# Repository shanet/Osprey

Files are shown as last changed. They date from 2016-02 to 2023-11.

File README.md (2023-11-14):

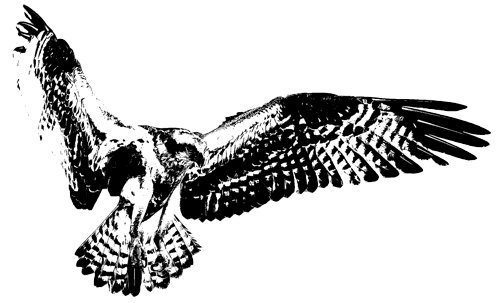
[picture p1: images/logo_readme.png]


Osprey
======

**Note: I am no longer active in rocketry and as such this repo is unmaintained. Everything here is fairly self-enclosed, however, so it should be possible to get running without too much trouble if you are interested in it.**

Osprey is a free and open source tracking, telemetry, and dual deployment system for amateur rocketry utilizing only off-the-shelf components. It consists of five major components:

0. [The microcontroller and associated sensors](docs/arm.md)
0. [The e-match igniter circuit](docs/igniter.md)
0. [The Android application for receiving data during a flight](docs/android.md)
0. [The desktop application for laptop-based analysis and debugging](docs/desktop.md)
0. [The launch report generation script for post-flight analysis](docs/reports.md) ([sample launch report](https://shanet.github.io/Osprey/))

The final assembled product, corresponding Android application, and launch report:

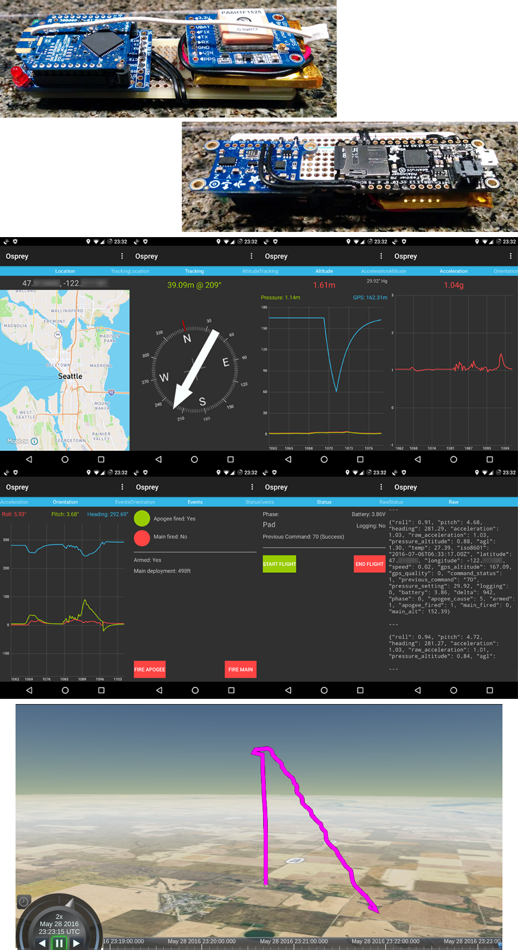
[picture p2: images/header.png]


The following data is collected:

| | | | |
|---|---|---|---|
|Latitude & longitude |Above ground level |ISO 8601 timestamp  |Battery voltage |
|Roll, pitch, heading |Pressure altitude |Integer timestamp |Temperature |
|Acceleration |GPS altitude & speed |Flight phase |Event fired flags |

All data is logged to an on-board microSD card and transmitted via radio to the Android application.

## High Level Build Overview

Osprey, by nature, is extremely DIY. This is necessary to achieve its goal of not using any custom printed hardware or non-free software. If you are not comfortable soldering your own circuits together or compiling software from source, this is not the project for you. In fact, it's quite likely, even inevitable, that something won't go as intended during a build. Those looking for a more plug'n'play solution should look elsewhere. For the adventurous out there, to fully construct everything follow these steps:

0. [Assemble the microcontroller and associated sensors](docs/arm.md)
0. [Assemble the igniter board](docs/igniter.md)
0. [Compile and upload the microcontroller software](docs/arm.md#software)
0. [Set the required radio configuration](docs/radio.md)
0. [Install the completed microcontroller, sensors, igniter, and switch to your e-bay sled](docs/assembly.md)
0. [Compile and install the Android application](docs/android.md)
0. [Review the usage section](docs/usage.md)
0. Do some ground tests, then stick it in a rocket and cross your fingers.

For everything else, see the documentation in the `docs` directory.

A write-up of some of Osprey's internals (Kalman filter, apogee detection, testing, etc.) is [available on my blog](https://shanetully.com/2016/07/inside-the-construction-of-an-amateur-rocketry-flight-computer).

## Roadmap

Some potential future additions:

* "Micro version" with only a processor, IMU, and battery for data logging purposes only.
* The 3D flight path playback in the launch report could be made more rich with the addition of altitude and flight phase data.
* Support for multiple flight stages.
* Reworking the igniter circuit to only need a single capacitor.
* Support for offline maps in the generated launch report webpage.

## Contributing

Pull requests, bug reports, and general questions are welcome. Additionally, suggestions on where the documentation can be made more clear are extremely useful. Log files and generated launch reports are appreciated as well for helping to improve the project and as a showcase.

## License

This program is free software: you can redistribute it and/or modify
it under the terms of the GNU General Public License as published by
the Free Software Foundation, either version 3 of the License, or
(at your option) any later version.

This program is distributed in the hope that it will be useful,
but WITHOUT ANY WARRANTY; without even the implied warranty of
MERCHANTABILITY or FITNESS FOR A PARTICULAR PURPOSE.  See the
GNU General Public License for more details.

You should have received a copy of the GNU General Public License
along with this program.  If not, see <http://www.gnu.org/licenses/>.

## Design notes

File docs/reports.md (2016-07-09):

## Launch Reports

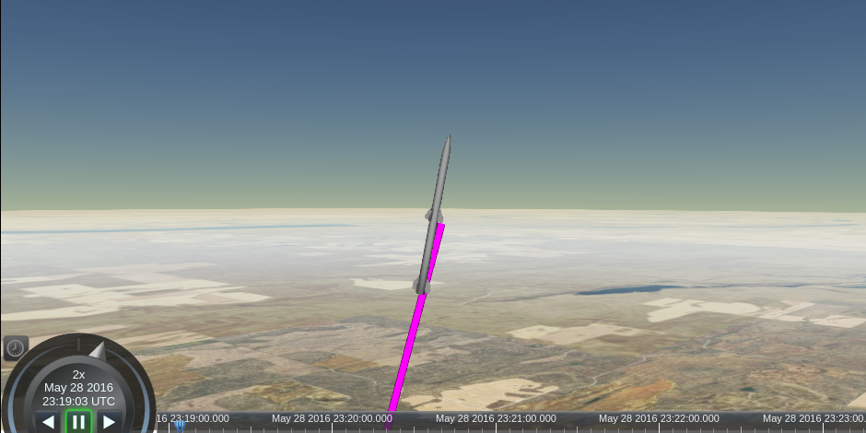
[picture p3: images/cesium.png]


A Ruby script to generate a self-contained, static HTML report of a launch from its log file is included. This allows for quick analysis of a flight including the following information:

| | | |
|---|---|---|
|Actual apogee |Calculated apogee |Apogee cause |
|Main chute target |Main chute actual |Average temperature |
|Flight time |Ascent time |Ascent rate |
|Descent time |Descent rate - drogue |Descent rate - main |

And:
* Graph of altitude, acceleration, and ground speed vs. time
* 3D view of flight path and rocket orientation (roll, pitch, heading)

[See here for a sample launch report](https://shanet.github.io/Osprey/)

### Dependencies

* Ruby (any recent version should do; no gems are required)

### Usage

```
$ reports/generate.rb
Usage: reports/generate.rb [input log] [output directory]
```

Then open `output_directory/report.html` in any web browser that supports WebGL. Chrome users: Chrome must be started with the `--allow-file-access-from-files` flag for the 3D playback to work.

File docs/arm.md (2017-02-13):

## Microcontroller & Sensors

All assembled, the total size is 9.5cm x 3.3cm x 2.8cm and weighs in at 50g.

### Hardware

The following hardware is used:

* [Adafruit Feather M0 Adalogger](https://www.adafruit.com/products/2796)
* [Adafruit Ultimate GPS](https://www.adafruit.com/products/746)
* [Adafruit 10-DOF IMU](https://www.adafruit.com/products/1604)
* [XBee Pro 900 Wire Antenna](http://www.mouser.com/ProductDetail/Digi-International/XBP9B-DMWT-002)
* [XBee Pro 900 RP-SMA Connector](http://www.mouser.com/ProductDetail/Digi-International/XBP9B-DMST-002)
* [Adafruit XBee Adapter Kit](https://www.adafruit.com/product/126)
* [SparkFun XBee Explorer Dongle](https://www.sparkfun.com/products/11697)
* [Adafruit 500mAh LiPo battery](https://www.adafruit.com/product/1578)
* [Adafruit Perma-Proto Half-size Breadboard PCB](https://www.adafruit.com/products/1609) (cut in half for use as a mounting board)
* Either an omnidirectional antenna or a Yagi antenna with an RP-SMA connector
* [3 position terminal block](https://www.adafruit.com/products/725)
* USB OTG if connecting to an Android device
* [Foam mounting tape to hold everything to the mounting board](https://www.amazon.com/3M-Scotch-Mounting-125-Inch-314/dp/B0007P5G8Y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)

**Note:** Adafruit is occasionally out of stock with their components. I have had good luck in the past finding them in stock at [Mouser](http://www.mouser.com).

### Wiring

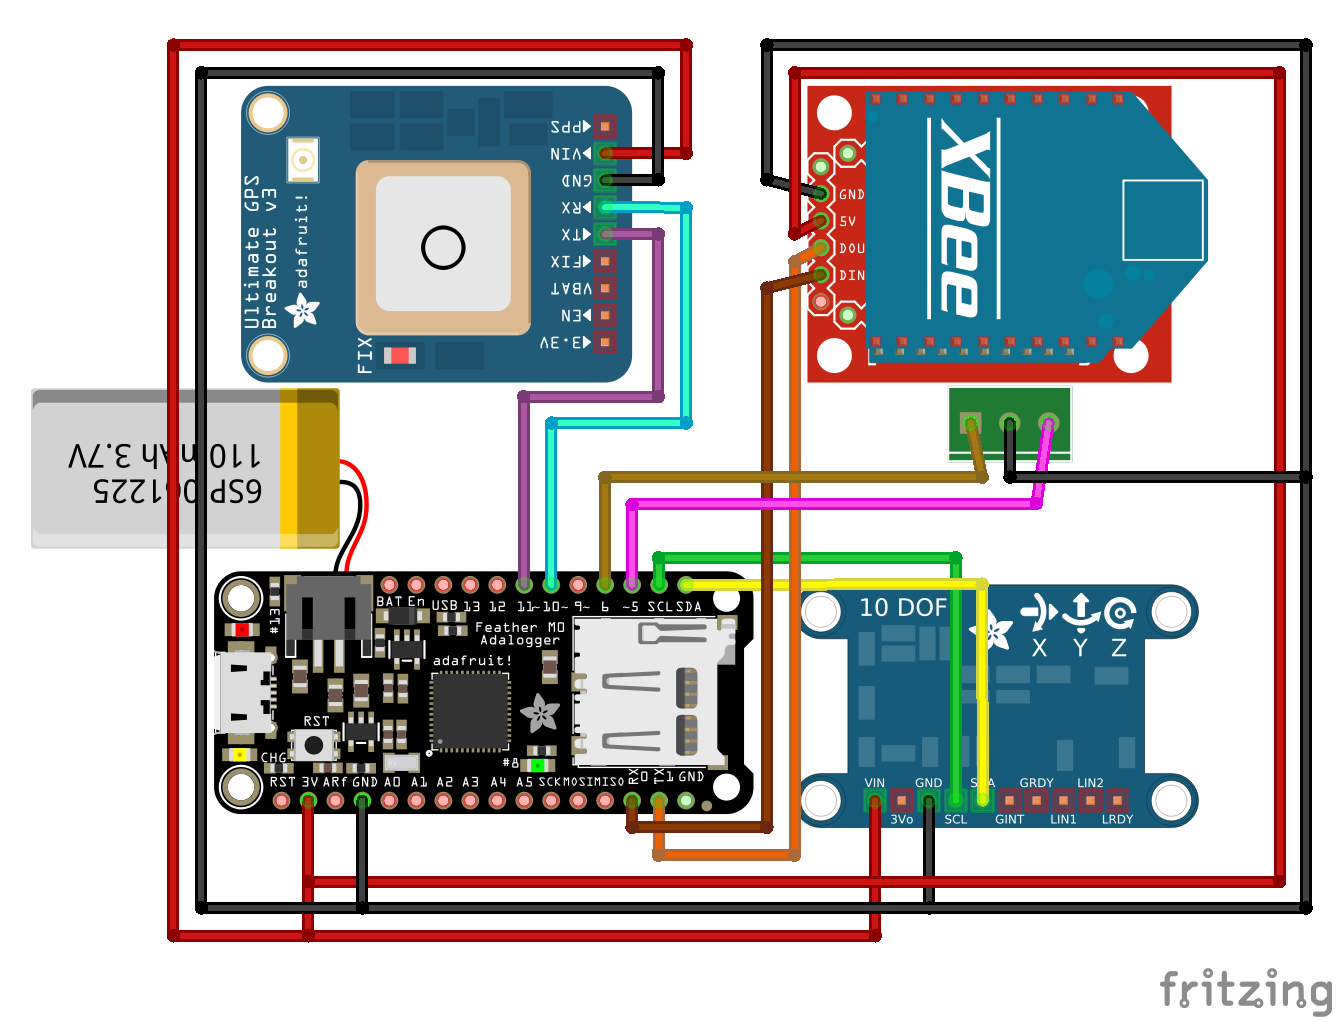
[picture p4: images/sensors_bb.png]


|Radio | GPS | IMU | Igniter terminal |
|---|---|---|---|
|Pin 1 -> RX | Pin 10 -> RX | SDA -> SDA  | Left -> Pin 6 |
|Pin 0 -> TX | Pin 11 -> TX | SCL -> SCL  | Center -> GND |
|3.3V -> Vin | 3.3V -> Vin  | 3.3V -> Vin | Right -> Pin 5 |
|GND -> GND  | GND -> GND | GND -> GND  | |

### Software

#### Dependencies

These instructions are for Linux (x86_64). See below for where to find instructions for other platforms. Do not ask for Windows support.

* Download and extract the [Adafruit SAMD library](https://github.com/adafruit/arduino-board-index/raw/gh-pages/boards/adafruit-samd-1.0.9.tar.bz2) to `~/.arduino15/packages/adafruit/hardware/samd/1.0.9`
* Download and extract the [ARM compiler](http://downloads.arduino.cc/gcc-arm-none-eabi-4.8.3-2014q1-linux64.tar.gz) to `~/.arduino15/packages/adafruit/tools/arm-none-eabi-gcc/4.8.3-2014q1`
* Download and extract [Bossac](http://downloads.arduino.cc/bossac-1.6.1-arduino-x86_64-linux-gnu.tar.gz) to `~/.arduino15/packages/adafruit/tools/bossac/1.6.1-arduino`.
* Download and extract [CMSIS](http://downloads.arduino.cc/CMSIS-4.0.0.tar.bz2) to `~/.arduino15/packages/adafruit/tools/CMSIS/4.0.0-atmel`.

Note: The archives above can be extracted whenever you'd like, but the paths at the top of the Makefile must be adjusted accordingly.

Alternatively, Adafruit has good instructions for getting the above set up with the help of the Arduino software. If not using Linux, this is most likely the easiest way to gather the dependencies.

For convenience, here's a list of commands to download each of the tarballs above and put them in the correct location:

```
mkdir -p ~/.arduino15/packages/adafruit/hardware/samd/1.0.9
mkdir -p ~/.arduino15/packages/adafruit/tools/arm-none-eabi-gcc/4.8.3-2014q1
mkdir -p ~/.arduino15/packages/adafruit/tools/bossac/1.6.1-arduino
mkdir -p ~/.arduino15/packages/adafruit/tools/CMSIS/4.0.0-atmel

curl --location https://github.com/adafruit/arduino-board-index/raw/gh-pages/boards/adafruit-samd-1.0.9.tar.bz2 | tar -xjf - --strip-components=1 --directory ~/.arduino15/packages/adafruit/hardware/samd/1.0.9
curl http://downloads.arduino.cc/gcc-arm-none-eabi-4.8.3-2014q1-linux64.tar.gz | tar -xzf - --strip-components=1 --directory ~/.arduino15/packages/adafruit/tools/arm-none-eabi-gcc/4.8.3-2014q1
curl http://downloads.arduino.cc/bossac-1.6.1-arduino-x86_64-linux-gnu.tar.gz | tar -xzf - --strip-components=1 --directory ~/.arduino15/packages/adafruit/tools/bossac/1.6.1-arduino
curl http://downloads.arduino.cc/CMSIS-4.0.0.tar.bz2 | tar -xjf - --strip-components=1 --directory ~/.arduino15/packages/adafruit/tools/CMSIS/4.0.0-atmel

```

#### Compiling & Uploading

```
$ cd arm
$ make
$ make upload
```

### Tests

```
$ cd arm
$ make test
$ make test_run # Don't re-compile, only run tests
```

#### Replaying flight from log

In some cases, it is useful to "replay" a flight from its associated log file. For example, when working on logic for apogee detection it is much easier and faster to replay the flight from an existing log file instead of doing actual test launches. To use this, simply place a log file at
```
arm/test/fixtures/replay.json
```
and then run the tests as normal. The output from the replayed flight will be printed to stdout in the usual log format.

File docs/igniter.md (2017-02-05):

## Igniter

Osprey uses a custom designed, capacitor-based igniter circuit with two channels and capable of being powered by a 3.7V lipo battery. **This is an optional component.** It is perfectly okay to simply skip this for use in a non-dual deployment or low power rocket. The microcontroller itself can fit inside a 1.65" diameter rocket which makes for a great standalone tracking system.

All assembled, the total size is 8.2cm x 2.5cm x 2.1cm and weighs in at 26g.

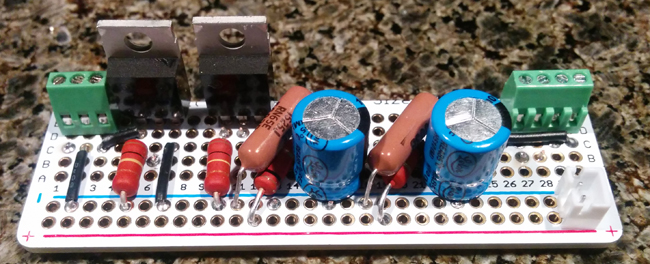
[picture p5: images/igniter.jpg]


### Hardware

* [30V 30A N-channel MOSFET x2](http://www.mouser.com/ProductDetail/NXP/PSMN022-30PL127/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)
* [1000uF capacitor x2](http://www.mouser.com/ProductDetail/Lelon/REA102M1ABK-1012P/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)
* [500k Ohm resistor x2](http://www.mouser.com/ProductDetail/Vishay/RN65E5003BB14/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)
* [100k Ohm resistor x2](http://www.mouser.com/ProductDetail/Vishay-BC-Components/PR02000201003JR500/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)
* [1k Ohm resistor x2](http://www.mouser.com/ProductDetail/Vishay-BC-Components/PR02000201001JR500/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)
* [3-position terminal block](http://www.mouser.com/ProductDetail/Adafruit/2136/)
* [4-position terminal block](http://www.mouser.com/Search/ProductDetail.aspx?qs=GURawfaeGuCecymQwHHL1g%3d%3d)
* JST-PH connector for battery
* [JST-PH Breakout board](https://www.adafruit.com/product/1862)
* [Magnetic switch](http://shop.featherweightaltimeters.com/product.sc?productId=33&categoryId=2).
** Magnets: I used a combination of both a [cube magnet](https://www.amazon.com/gp/product/B0012DNFP6/ref=oh_aui_search_detailpage?ie=UTF8&psc=1) and [circular magnets](https://www.amazon.com/gp/product/B008H40U10/ref=oh_aui_search_detailpage?ie=UTF8&psc=1).

### Switch

Any switch will work; I used a magnetic switch for the ability to easily turn the electronics on/off without the need to put a large access hole in the e-bay. If going this route, you may need a more/less powerful magnet depending on the diameter of the rocket. The magnets listed above worked well for a 2.56" diameter rocket with the switch placed roughly in the center.

The switch is connected to the JST breakout board which is then connected to the igniter with a JST cable. This allows for all components to be swapped out independent of one another.

### Schematic & Wiring

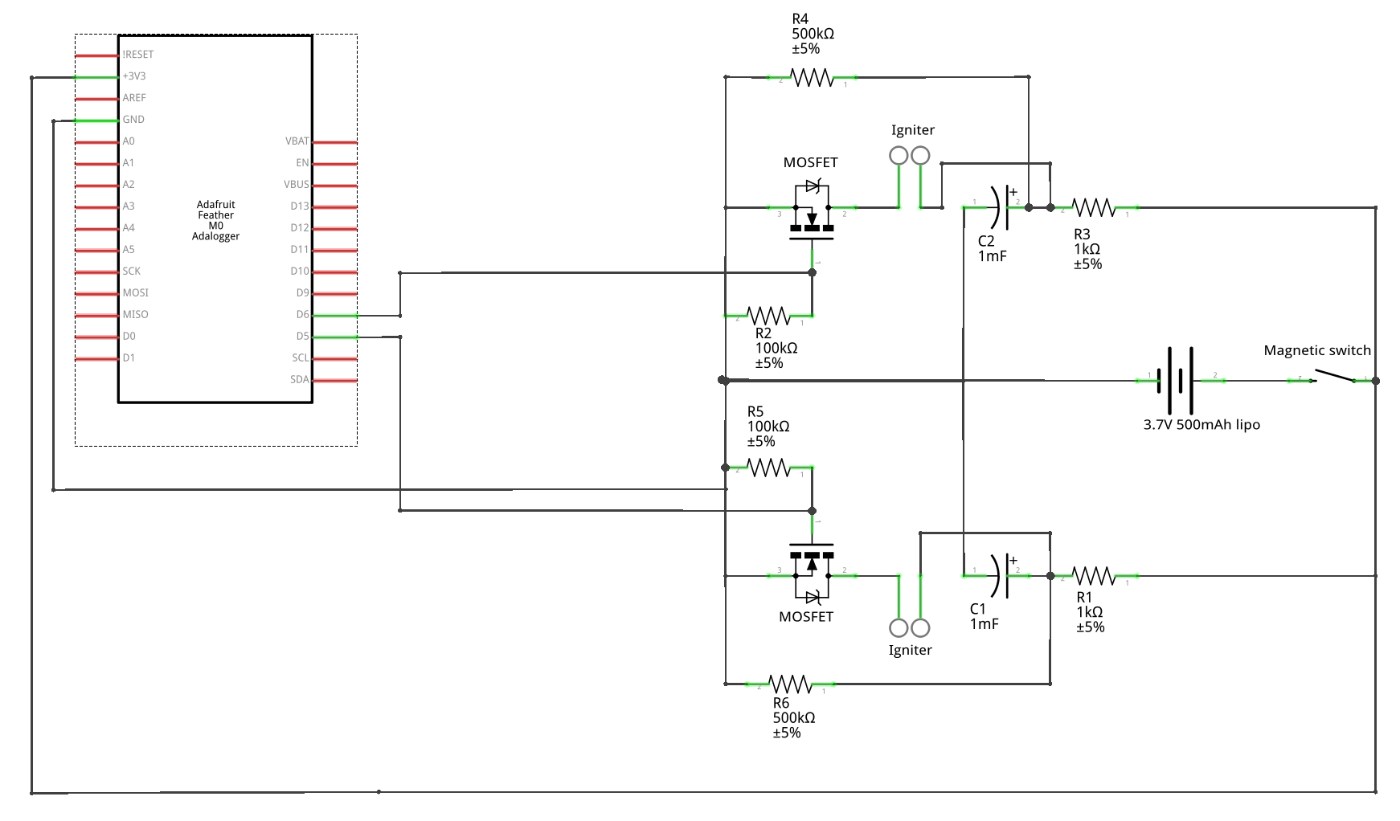
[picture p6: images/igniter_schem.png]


It's a tight fit, but it is possible to fit the igniter circuit on the other half of the proto-board used for the microcontroller and sensors as such:

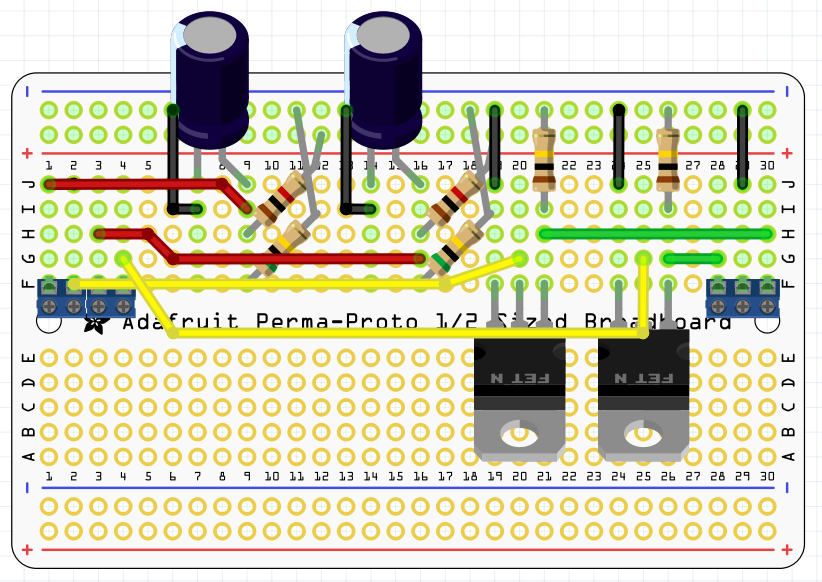
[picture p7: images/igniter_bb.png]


The JST connector is not shown on this diagram, but it would be placed directly on the positive and negative power rails.

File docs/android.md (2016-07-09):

## Android Application

The Android app is the main method of interfacing with the rocket during flight and during recovery. It contains a display of all data from the rocket as well as the ability to issue commands to the rocket. Moreover, it tracks the rocket's location and continuously calculates the distance and direction from the device's location to the rocket.

A pre-built APK is not available in order to preserve the author's sanity that would surely be lost from publishing an app on the Play store.

### Dependencies

Install Android Studio or at least the Android command line tools from https://developer.android.com/studio/index.html#downloads.

In Osprey's directory, you may have to create a file, `android/local.properties`, with the following content:
```
sdk.dir=/path/to/android/sdk
```

### Compiling

```
$ cd android
$ ./gradlew assembleDebug
```

### Installing

ADB must be enabled on the target device before installing. See https://developer.android.com/studio/command-line/adb.html#Enabling for instructions.

```
$ cd android
$ ./gradlew installDebug
```

### Usage

With the radio plugged in and GPS enabled, start the app. There are eight main views:

* Location: A map with the current rocket location, device location, flight path of rocket, and path from current device location to the rocket. The options menu contains options to change the map style, show the last known location of the rocket, save maps for offline use, and track a given pair of coordinates.
* Tracking: The distance and relative bearing to the rocket's current location as well a compass and unnecessarily large arrow that points towards the rocket. The options menu contains options to show the last known location of the rocket and track a given pair of coordinates.
* Altitude: A graph of the above ground level, pressure altitude, and GPS altitude along with the pressure setting and an option to set it.
* Acceleration: A graph of the combined X, Y, and Z axes acceleration.
* Orientation: A graph of the roll, pitch, and heading angles.
* Events: A display of which events have fired, if the igniter is armed, and the altitude the main chute is set to deploy at. Also here are the override buttons to manually fire the apogee and main chutes. The options menu contains options to arm the igniter and set the main chute deployment altitude.
* Status: The phase the rocket is in, the most recent command and battery voltage. The buttons for the start and end flight commands are also found here.
* Raw: The last 100 lines of the raw radio log. This is useful if the rocket goes out of range of the receiver and sends corrupted JSON strings. It may be possible to manually extract some useful data from these.

The full log file displayed in the Raw view can be found through a file manager at `/sdcard/Android/data/com.shanet.osprey/files/osprey.log`.

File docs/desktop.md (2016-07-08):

## Desktop Application

The desktop application is primarily used during development and for debugging purposes as it's not usually practical to carry a laptop around at the launch site. Two interfaces are available, a graphical Qt interface with graphing capabilities, and a console curses UI.

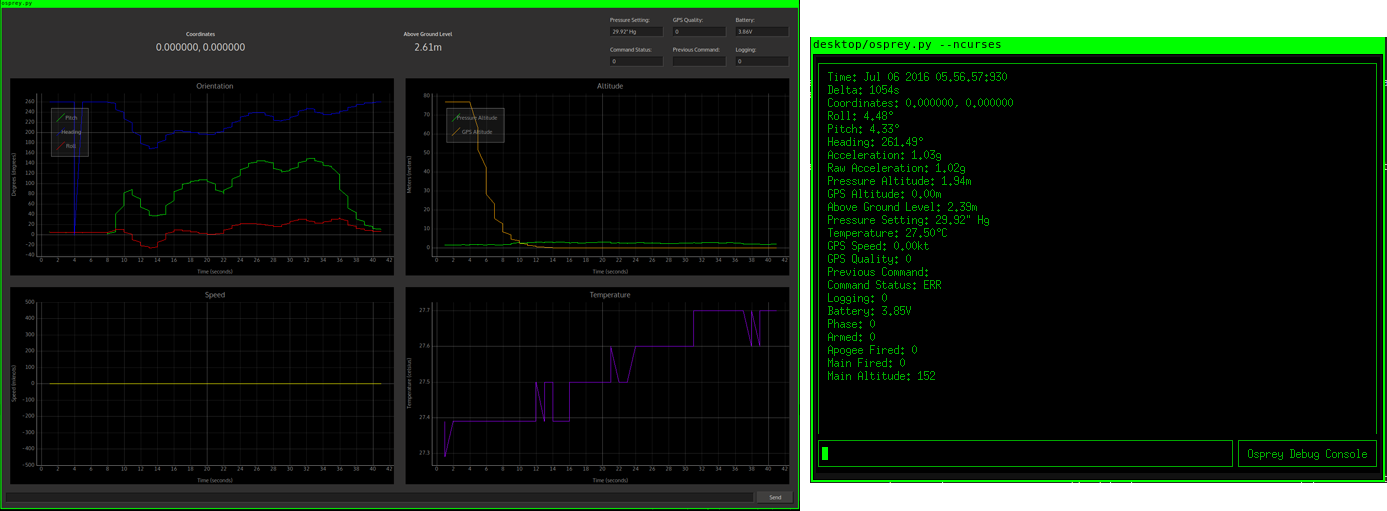
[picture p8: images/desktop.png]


### Dependencies

* Python 3
* Python packages:
  * PySide
  * Curses

### Usage

```
$ desktop/osprey.py --help
usage: osprey.py [-h] [-d [DEVICE]] [-b [BAUD]] [-n]

optional arguments:
  -h, --help            show this help message and exit
  -d [DEVICE], --device [DEVICE]
                        Block device to read from
  -b [BAUD], --baud [BAUD]
                        Baud rate to read from block device with
  -n, --ncurses         Use the Ncurses UI
```

* Qt: `$ desktop/osprey.py`
* Curses: `$ desktop/osprey.py --ncurses`

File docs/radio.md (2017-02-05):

## Radio Configuration

Xbee Pro radios are used for communication between the rocket and the ground. Xbee Pros were chosen because of their increased range. Despite being more expensive, the cost is more than made up for simply by being able to recover a rocket due to the increased range. However, keep in mind that 900mHz is still line of sight. If your rocket lands on the other side of a hill, the signal will be temporarily lost. A directional antenna is also highly recommended.

The radios themselves require some configuration, however, config files are provided so it's just a matter of setting two fields and uploading them to the radios.

0. Download, install, and run the [XCTU software](http://www.digi.com/products/xbee-rf-solutions/xctu-software/xctu).
0. With the radio plugged in via USB, select "Discover Radios" from the top left.
0. Select the found radio and in the right column, scroll down to the "Addressing" section and copy/write down the "SH - Serial Number High" and "SL - Serial Number Low" fields.
0. Repeat steps 1-3 for the other radio.
0. Select the found radio and then click "Profile" and select "Load configuration profile."
  * [Config for the rocket radio](/config/radio_rocket_config.xml)
  * [Config for the ground radio](/config/radio_ground_config.xml)
0. In the right column under the "Addressing" section, fill in the value from the "SH - Serial Number High" field from the opposite radio into the "DH - Destination Address High" field. Do the same for the "SL - Serial Number Low" value and the "DL - Destination Address Low" field.
0. Write the config to the radio by clicking the "Write" button.
0. Repeat steps 5-7 for the other radio.

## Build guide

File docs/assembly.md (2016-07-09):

## Final Assembly

A variety of switches may be used. For simplicity, a single switch for both the microcontroller and igniter is used here. Below is a photo of everything installed to a 2.6" e-bay sled.

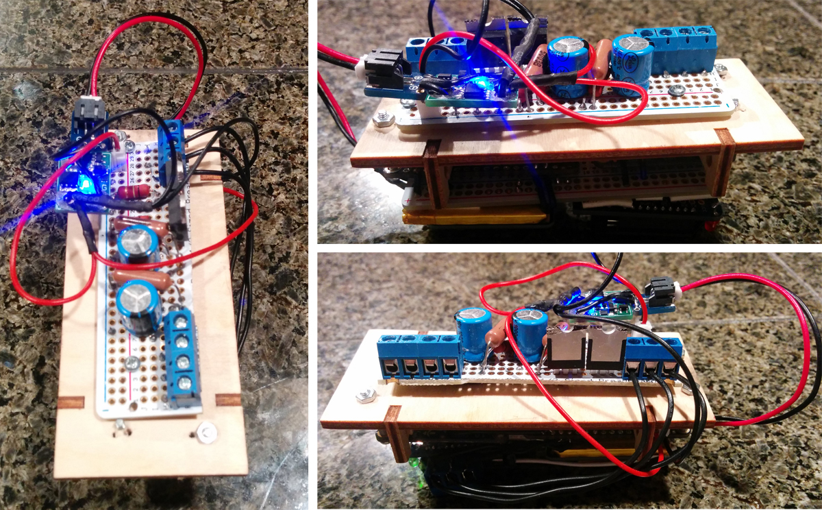
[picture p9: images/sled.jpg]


In short, the final assembly includes:

* Connect the igniter to the micrcontroller via the terminal blocks.
* Connect the battery to the switch and the switch to the igniter and microcontroller.
  * JST wires and [a JST breakout board](https://www.adafruit.com/product/1862) are used in the photo above to make for quick connects/disconnects.
* Your local hardware store will have machine screws and nuts that fit in the mount holes on the microcontroller and IMU for mounting to the e-bay sled.
* Two holes were drilled through igniter's PCB for mounting in the photo above.

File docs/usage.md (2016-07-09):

## Overall Usage (ie. actually flying the thing)

Once everything is built, soldered, compiled, and running, the hard part is over. Usage is relatively straightforward, but there are some points of interest to be aware of:

* The battery used is a 3.7V lipo. When fully charged, it will run at slightly above 4V, quickly dropping down to ~3.7V, holding that voltage for a while, then dropping again before dying at around 3.3V. **It is critical to understand that the igniter circuit has not been tested successfully below 3.6V**. While the processor and sensors will work at or below this voltage, it is highly recommended to never launch on a battery that is below 3.7V. Fully charged batteries are clearly ideal simply for maximum battery life in the event of a difficult recovery.
* The microSD card should be an SDHC card formatted as FAT32. Some cards (especially old ones) may require too much current during writes than the microcontroller is capable of providing resulting in board resets.
* Issuing the "start flight" command will arm the igniter. Never do this until the rocket is on the pad and pointed up, but before the motor igniter is inserted.
* The "end flight" command will stop logging and flush all data to the SD card. It is highly recommended to issue this command upon rocket recovery to avoid loss of a log file.
  * In the event that a log file is lost from the filesystem, a data recovery program may be able to recover it. [PhotoRec](http://www.cgsecurity.org/wiki/PhotoRec) is a good option for this.

In short, the process for usage is as follows:

0. Connect microcontroller and sensors to the igniter circuit
0. Connect e-matches to igniter circuit
0. Connect battery to switch
0. With rocket on the pad, use switch to turn on the boards
0. From the Android app, confirm data is being received
0. Issue the "start flight" command and verify the following:
  * Above ground level is 0m or nearly 0m
  * Flight phase is "pad"
  * Igniter is armed
  * Logging is enabled
  * Battery is at least 3.7V
  * GPS has valid coordinates

And you're ready to fly!

### Commands

* Start flight: Shortcut for setting phase to pad, zeroing sensors, arming igniter, and enable logging.
* End flight: Shortcut for disable logging and disarm igniter. Note: In order to prevent data loss from not closing the log file, it's important to remember to issue the end flight command immediately following rocket recovery.
* Set pressure setting: Change the pressure setting from the default of 29.92"Hg to the current reading. This is only necessary for a correct pressure altitude, but will not affect the above ground level value (provided that the pressure setting is not changed mid-flight). The pressure setting will continuously vary, but the current reading may be obtained from the [METAR of your local airport](https://aviationweather.gov/metar).
* Zero: Zero the above ground level and relative timestamp counter.
* Start logging: Begin logging data points to a new log file on the SD card.
* End logging: Stop logging data points to the log file on the SD card.
* Set event: Set the altitude at which the given event will fire.
* Fire event: Immediately fire the e-match connected to the igniter for the given event. Note: The igniter must be armed in order for it to fire.
* Arm igniter: Arm the igniter to allow it to be fired.
* Disarm igniter: Disarm the igniter to not allow it to be fired.

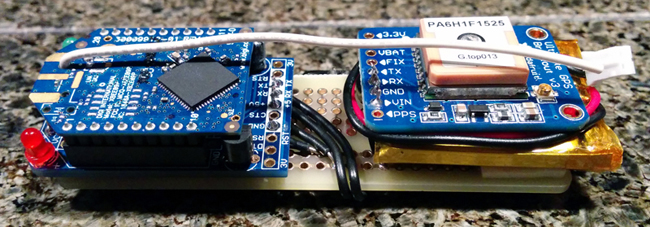
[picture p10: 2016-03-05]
images/assembled_1.jpg

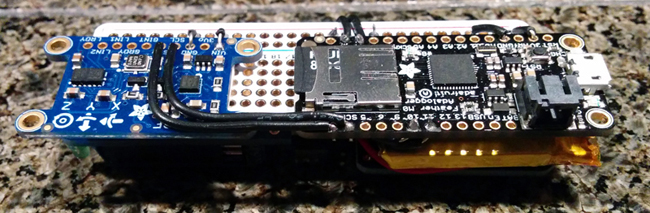
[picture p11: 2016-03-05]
images/assembled_2.jpg

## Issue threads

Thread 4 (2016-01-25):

Increase numpy array size

shanet, 2016-01-25:
Current size is 1000 elements which is too small for long runs of the program.

shanet, 2016-01-25:
This should also include handling the case of a full buffer.

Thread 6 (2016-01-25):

Allow multiple logs

shanet, 2016-01-25:
Current log is overwritten on each run. The filenames should have a timestamp in them to allow for multiple logs and to give info about when the log is from in the filename.

shanet, 2016-06-23:
On-board logging is sufficient.

Closed 2016-06-23.

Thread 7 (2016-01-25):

Add error handling in Qt UI

shanet, 2016-01-25:
The Qt UI does not handle errors such as invalid JSON or a failure to init a sensor.

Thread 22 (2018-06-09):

500k resistors on igniter board?

marccardinal, 2018-06-09:
Good afternoon,

Can you explain the purpose of the 500k ohm resistors on the igniter board? They seem to be applying a constant (but minimal) load on the battery and look optional no?

Thanks!

shanet, 2018-06-10:
That's right, they are not strictly required. They are present to act as a safety check on slowly discharging the capacitors after the battery is disconnected to prevent inadvertent ignitions of the igniters.

marccardinal, 2018-06-11:
Oh that makes sense! Thanks for the explanation :)

Closed 2018-06-11.

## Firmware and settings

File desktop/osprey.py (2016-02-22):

#! /usr/bin/env python3

import sys
import signal
import argparse

import constants

from ncurses import OspreyNcurses
from qt import OspreyQt

ui = None

def main():
  signal.signal(signal.SIGINT, signalHandler)
  args = parseCmdLineArgs()

  if args.ncurses:
    ui = OspreyNcurses(args.device, args.baud)
  else:
    ui = OspreyQt(args.device, args.baud)

  ui.start()
  sys.exit(0)

def parseCmdLineArgs():
    argvParser = argparse.ArgumentParser()

    argvParser.add_argument('-d', '--device', dest='device', nargs='?', type=str, default=constants.DEFAULT_BLOCK_DEVICE, help='Block device to read from')
    argvParser.add_argument('-b', '--baud', dest='baud', nargs='?', type=int, default=constants.DEFAULT_BAUD_RATE, help='Baud rate to read from block device with')
    argvParser.add_argument('-n', '--ncurses', dest='ncurses', default=False, action='store_true', help='Use the Ncurses UI')

    args = argvParser.parse_args()

    return args

def signalHandler(signal, frame):
  if ui is not None:
    ui.stop()

  sys.exit(0)

if __name__ == '__main__':
  main()

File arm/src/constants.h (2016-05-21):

#define NO_DATA -1
#define MERCURY_TO_HPA_CONVERSION 33.8638866667
#define DEFAULT_PRESSURE_SETTING 29.92f // inches of mercury
#define MS2_TO_G 0.101971621

#define COMMAND_ZERO_SENSORS 0
#define COMMAND_SET_PRESSURE 1
#define COMMAND_ENABLE_LOGGING 2
#define COMMAND_DISABLE_LOGGING 3
#define COMMAND_START_FLIGHT 4
#define COMMAND_END_FLIGHT 5
#define COMMAND_SET_EVENT 6
#define COMMAND_FIRE_EVENT 7
#define COMMAND_ARM_IGNITER 8
#define COMMAND_DISARM_IGNITER 9

#define COMMAND_ERR 0
#define COMMAND_ACK 1

// Flight phases
#define PAD 0
#define BOOST 1
#define COAST 2
#define DROGUE 3
#define MAIN 4
#define LANDED 5

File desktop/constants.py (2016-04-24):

DEFAULT_BLOCK_DEVICE = '/dev/ttyUSB0'
DEFAULT_BAUD_RATE = 115200

DEFAULT_LABEL = 'N/A'
NUMPY_ARRAY_SIZE = 1000

RIGHT_DATA_DISPLAYS_PER_ROW = 3
GRAPHS_PER_ROW = 2

DISPLAYS = {
  'time': {
    'label': 'Time (UTC)',
    'field': 'timestamp',
  },
  'coordinates': {
    'label': 'Coordinates',
    'field': 'coordinates',
  },
  'roll': {
    'label': 'Roll',
    'field': 'roll',
    'units': '\xb0',
    'color': 'FF0000',
  },
  'pitch': {
    'label': 'Pitch',
    'field': 'pitch',
    'units': '\xb0',
    'color': '00FF00',
  },
  'heading': {
    'label': 'Heading',
    'field': 'heading',
    'units': '\xb0',
    'color': '0000FF',
  },
  'pressure_altitude': {
    'label': 'Pressure Altitude',
    'field': 'pressure_altitude',
    'units': 'm',
    'color': '00FF00',
  },
  'gps_altitude':{
    'label': 'GPS Altitude',
    'field': 'gps_altitude',
    'units': 'm',
    'color': 'FFAA00',
  },
  'agl': {
    'label': 'Above Ground Level',
    'field': 'agl',
    'units': 'm',
  },
  'pressure_setting': {
    'label': 'Pressure Setting',
    'field': 'pressure_setting',
    'units': '" Hg',
  },
  'temp': {
    'label': 'Temperature',
    'field': 'temp',
    'units': '\xb0C',
    'color': '9900FF',
  },
  'speed': {
    'label': 'GPS Speed',
    'field': 'speed',
    'units': 'kt',
    'color': 'FFFF00',
  },
  'gps_quality': {
    'label': 'GPS Quality',
    'field': 'gps_quality',
  },
  'previous_command': {
    'label': 'Previous Command',
    'field': 'previous_command',
  },
  'command_status': {
    'label': 'Command Status',
    'field': 'command_status',
  },
  'battery': {
    'label': 'Battery',
    'field': 'battery',
    'units': 'V',
  },
  'logging': {
    'label': 'Logging',
    'field': 'logging',
  },
}

LEFT_DATA_DISPLAYS = [
  DISPLAYS['coordinates'],
  DISPLAYS['agl'],
]

RIGHT_DATA_DISPLAYS = [
  DISPLAYS['pressure_setting'],
  DISPLAYS['gps_quality'],
  DISPLAYS['battery'],
  DISPLAYS['command_status'],
  DISPLAYS['previous_command'],
  DISPLAYS['logging'],
]

GRAPHS = [
  {
    'title': 'Orientation',
    'displays': [
      DISPLAYS['roll'],
      DISPLAYS['pitch'],
      DISPLAYS['heading'],
    ],
    'labels': {'left': ('Degrees', 'degrees'), 'bottom': ('Time', 'seconds')},
  },
  {
    'title': 'Altitude',
    'displays': [
      DISPLAYS['gps_altitude'],
      DISPLAYS['pressure_altitude'],
    ],
    'labels': {'left': ('Meters', 'meters'), 'bottom': ('Time', 'seconds')},
  },
  {
    'title': 'Speed',
    'displays': [
      DISPLAYS['speed'],
    ],
    'labels': {'left': ('Speed', 'knots'), 'bottom': ('Time', 'seconds')},
  },
  {
    'title': 'Temperature',
    'displays': [
      DISPLAYS['temp'],
    ],
    'labels': {'left': ('Temperature', 'celsius'), 'bottom': ('Time', 'seconds')},
  },
]

COMMAND_ZERO = {'name': 'zero', 'value': 0, 'arg': False}
COMMAND_SET_PRESSURE = {'name': 'pressure', 'value': 1, 'arg': True}
COMMAND_ENABLE_LOGGING = {'name': 'enable_logging', 'value': 2, 'arg': False}
COMMAND_DISABLE_LOGGING = {'name': 'disable_logging', 'value': 3, 'arg': False}
COMMAND_START_FLIGHT = {'name': 'start_flight', 'value': 4, 'arg': False}
COMMAND_END_FLIGHT = {'name': 'end_flight', 'value': 5, 'arg': False}
COMMAND_SET_EVENT = {'name': 'set_event', 'value': 6, 'arg': True}
COMMAND_FIRE_EVENT = {'name': 'fire_event', 'value': 7, 'arg': True}
COMMAND_ARM_IGNITER = {'name': 'arm', 'value': 8, 'arg': False}
COMMAND_DISARM_IGNITER = {'name': 'disarm', 'value': 9, 'arg': False}

COMMANDS = [
  COMMAND_ZERO,
  COMMAND_SET_PRESSURE,
  COMMAND_ENABLE_LOGGING,
  COMMAND_DISABLE_LOGGING,
  COMMAND_START_FLIGHT,
  COMMAND_END_FLIGHT,
  COMMAND_SET_EVENT,
  COMMAND_FIRE_EVENT,
  COMMAND_ARM_IGNITER,
  COMMAND_DISARM_IGNITER,
]

COMMAND_ERR = 0
COMMAND_ACK = 1

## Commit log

2015-11-29 add accelerometer, magnetometer, barometer, and thermometer sensors
2015-11-30 move sensor functions to objects
2015-12-18 add radio sensor
2015-12-19 write data sent via radio directly to UART register
2015-12-19 send sensor data as JSON
2015-12-21 add python curses program to read and parse data from arduino and send basic commands to arduino
2015-12-25 move arduino files to subdirectory and switch makefiles
2015-12-25 add python program for sending/receiving data to/from arduino
2015-12-28 add arduino bin and python cache files to gitignore
2015-12-28 fix #2: add status window in lower right corner
    [osprey.py]
2015-12-28 fix #3: Backspace doesn't work in the curses input box
    [osprey.py]
2015-12-31 move ncurses UI to own file in preparation for Qt UI and add command line args for block device and baud rate
2015-12-31 move reading serial device and parsing data to separate class
2016-01-06 use timestamp from arduino as time data on x axis in graphs
2016-01-25 decrease arduino delay between loops
2016-01-25 change graphs dict to array to ensure correct ordering
    [constants.py]
2016-02-09 move from AVR to ARM architecture
2016-02-22 add basic wiring info to README
2016-02-22 fix #13: measure battery voltage
    [ncurses.py]
2016-02-22 fix #14: use RTC for tracking seconds since boot
    [ncurses.py]
2016-02-22 fix infinite loop of processing current command
    [gps.cpp, gps.h]
2016-02-22 make sensor init function pure virtual
2016-03-03 add xbee usb vendor and product ids to device_filter
2016-03-05 add basic documentation to README
    [wiring.fzz]
2016-04-23 fix #10: implement kalman filter on accelerormeter, barometer, and gps data
    [gps.cpp, gps.h]
2016-04-23 add clear ground track option to location fragment
2016-04-23 replace kalman filter on gps coordinates with input sanitization function
    [gps.cpp, gps.h]
2016-04-24 add arm/disarm igniters command
2016-04-24 add arm/disarm commands to events fragment and add labels to status fragment displays
2016-04-24 make fire buttons red
2016-05-02 make status UI pretty and move pressure setting display/set to altitude fragment
2016-05-18 add test framework and some basic tests
2016-05-18 fix igniter not being armed when issuing start flight command
    [main.cpp]
2016-05-21 add tests for start flight, end flight, set pressure, and set event altitude commands
2016-06-17 display radio log in raw fragment instead of current message
2016-06-23 fix #19: use constants for commands
    [main.cpp, main.h]
2016-07-05 use roll, pitch, and heading info to show 3d model of rocket in launch report
2016-07-05 use bounding sphere of flight path for default camera position
2016-07-08 finish README documentation
    [igniter.fzz, sensors.fzz, wiring.fzz]
2016-07-08 add link to sample launch report
2017-02-06 update igniter wiring diagram
    [igniter.fzz]
2017-02-13 add commands for downloading and extracting ARM dependencies
2017-02-14 change console rule to use radio device
